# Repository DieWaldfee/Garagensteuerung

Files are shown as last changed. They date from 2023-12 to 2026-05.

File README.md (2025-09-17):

# Garagensteuerung
Steuerung eines Garagentorantriebs (Platine und Software) via Relaistrigger

### Beschreibung der Funktion:
Garagentorantriebe haben einen potentialfreien Relais-Kontakt. Wird dieser gebrückt, so wird der Antrieb aktiviert für eine Öffnen/Schließen -> das Tor fährt auf den nächsten Anschlag (oben oder unten). Wo das Tor aktuell steht und welche Richtung die Fahrt nehmen wird ist so nicht sensierbar.<br>
Im dazugekörigen blockly-Skript für ioBroker wird daher geprüft, welcher Endanschlag angefahren wird, um ggf. über einen weiteren Trigger (Triggerimpuls über das Relais) das Tor in die gewünschte Position zu bringen. Eine weitere Funktion ist - analog zu Rolladensteuerungen - eine Behanghöhe einzustellen. die wird über die Öffnungszeit / Schließzeit bestimmt -> 10% Behanghöhe entspricht damit 10% Öffnungszeit bis das Relais den Trigger zum stoppen des Torantriebs sendet- bzw. 90% Schließzeit, sollte das Tor am oberen Anschlag sein. (steht das Tor irgendwo, dann wird zuerst ein Anschlag angefahren, um dann den Behang einzustellen).

### Hardware:
Die Platine ist in dieser Version für eine Lochrasterplatine ausgelegt -> Leiterbahnen können mit einem Draht und Lötzinn erstellt werden. Dies ermöglicht es eigentlich jedem, der einen Lötkolben sein Eigen nennt es einfach nachzubauen :-) Die Eagle-Dateien liegen im Repository. Ein Überblick gibt das Fritzing-File. <br>
An der Platine können 4 Reed-Kontakte angeschlossen werden (oberer und unterer Anschlag, sowie zwei optionale Positionen). Über die Reedkontakte "Oben und Unten" wird die aktuelle Position des Tors bestimmt. Ein Relais dient dem Triggern des Garagenantriebs. Die STromversorgung kann entweder über ein Mini-Netzteil, oder einfach über ein USB-Netzteil realisiert werden (Letzteres ist bei mir im Einsatz). Drei LEDS zeigen ggf. Fehler, das Senden von MQTT-Botschaften und generell den Betrieb an. Optional kann ein DS18B20-Temperatursensor angeschlossen werden, sollte die Garagentemperatur von Interesse sein (weil der Wohnwagen dort steht, oder die Pflanzen überwintern sollen...).

### Software:
Der ESP32 benötigt natürlich seine Software. Das C++-File liegt im entsprechenden Verzeichnis und muss bezüglich MQTT-Broker-Account und Adresse angepasst werden. Zusätzlich ist natürlich auch das WiFi-Passwort und die IP-Adresse zu setzen. Danach kann das File z.B. mit der Arduino-IDE auf den ESP32DevKitV4-Modul aufgespielt werden. Compile und Upload brauchen nur ein paar Sekunden. Nach dem Start des ESP32 versucht der ESP32 den MQTT-Broker zu erreichen und übermittelt zyklisch den Status. Das angehängte blockly-Skript für den ioBroker liest die Botschaften aus und steuert das Tor an. Hier sind die Funktionen TorZu(um 23Uhr)... verortet. Der gesendete Torzustand kann im ioBroker zur Visualisierung verwendet werden. Ich steure den Telegramadapter an, sollte z.B. das Tor um 23Uhr nicht zu schließen sein (weil z.B. mein Sohn das Fahrad voll in den Fahrweg des Tores gestellt hat...).

### Abhängigkeiten:
OneWire.h:_____________OneWire by Jim Studt, Tom Pollard, Robin James... v2.3.8 (über Arduino IDE)<br>
DallasTemperature.h:___DallasTemperature by Miles Burton v4.0.3 (über Arduino IDE)<br>
WiFi.h:________________Arduino IDE<br>
WiFiClient.h:__________Arduino IDE<br>
PubSubClient.h:________PubSubClient by Nick O'Leary v2.8 (über Arduino IDE)<br>
esp_task_wdt.h:________Espressif IDE<br>

### Board ESP32
esp32 by Espressif Systems v1.0.6 (über Arduino IDE)<br>
Getestet habe ich auch v2.0.5<br>

### Benötigte Hardware:
* Relais <a href="https://www.amazon.de/gp/product/B0B5816YJ7/ref=ppx_yo_dt_b_search_asin_image?ie=UTF8&th=1"> Amazon </a> oder <a href="https://www.az-delivery.de/products/relais-modul"> AZ Delivery </a>
* ESP32 Dev Kit V4 <a href="https://www.azdelivery.de/products/esp-32-dev-kit-c-v4"> AZ Delivery </a>
* optional Temperatursensoren DS18B20 <a href="https://www.az-delivery.de/products/2er-set-ds18b20-mit-3m-kabel"> AZ Delivery </a>
* JST-Buchse <a href="https://www.amazon.de/gp/product/B0B2R99X99/ref=ppx_yo_dt_b_search_asin_title?ie=UTF8&psc=1"> Amazon </a>
* Klemmbuchse <a href="https://www.amazon.de/gp/product/B087RN8FDZ/ref=ppx_yo_dt_b_search_asin_title?ie=UTF8&th=1"> Amazon </a>
* Widerstände 4,7kOhm, 220 Ohm, 330 Ohm, Led grün, gelb und rot Amazon / eBay / Conrad...
* Levelshifter (3.3V <-> 5V)  <a href="https://www.amazon.de/RUNCCI-YUN-Pegelwandler-Converter-BiDirektional-Mikrocontroller/dp/B082F6BSB5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"> Amazon </a>
* Reed-Kontakte <a href="https://www.amazon.de/schwarz-Sicherheitskontaktsensor-magnetischer-Reed-Schalter-T%C3%BCrsensor/dp/B07Z4NCWDD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)"> Amazon </a>
* USB-Netzteil Amazon / eBay / Conrad...
* optional: Platinennetzteil AC-05-3    <a href="https://www.azdelivery.de/products/copy-of-220v-zu-5v-mini-netzteil"> AZ-Delivery </a>
* MC1490P (debouncer) auf Sockel, wenn gewünscht <a href="https://www.ebay.de/itm/201551880799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"> eBay </a>
* Kondensatoren <a href="https://www.amazon.de/AUKENIEN-Kondensator-Kondensatoren-Keramikkondensator-Kit/dp/B09NLZBC7R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"> Amazon </a>

**Haftungsausschluss**<br>
Deutsch: Dieses Projekt arbeitet mit Netzspannung (220 V) und darf ausschließlich von qualifiziertem Fachpersonal aufgebaut, installiert und betrieben werden. Durch die anliegende Spannung besteht Lebensgefahr! Fehler in Schaltung oder Software können zu Sachschäden (z. B. an Gebäude oder Heizung) oder zu gefährlichen Situationen für Leib und Leben führen. Nutzung auf eigene Gefahr – jegliche Haftung wird ausgeschlossen.
<br>
English: This project operates with mains voltage (220 V) and must only be assembled, installed, and operated by qualified professionals. The present voltage poses a risk of fatal electric shock! Errors in circuitry or software may cause property damage (e.g., to buildings or heating systems) or create life-threatening situations. Use at your own risk – any liability is disclaimed.

<br>(Bezugslinks füge ich später noch hinzu)

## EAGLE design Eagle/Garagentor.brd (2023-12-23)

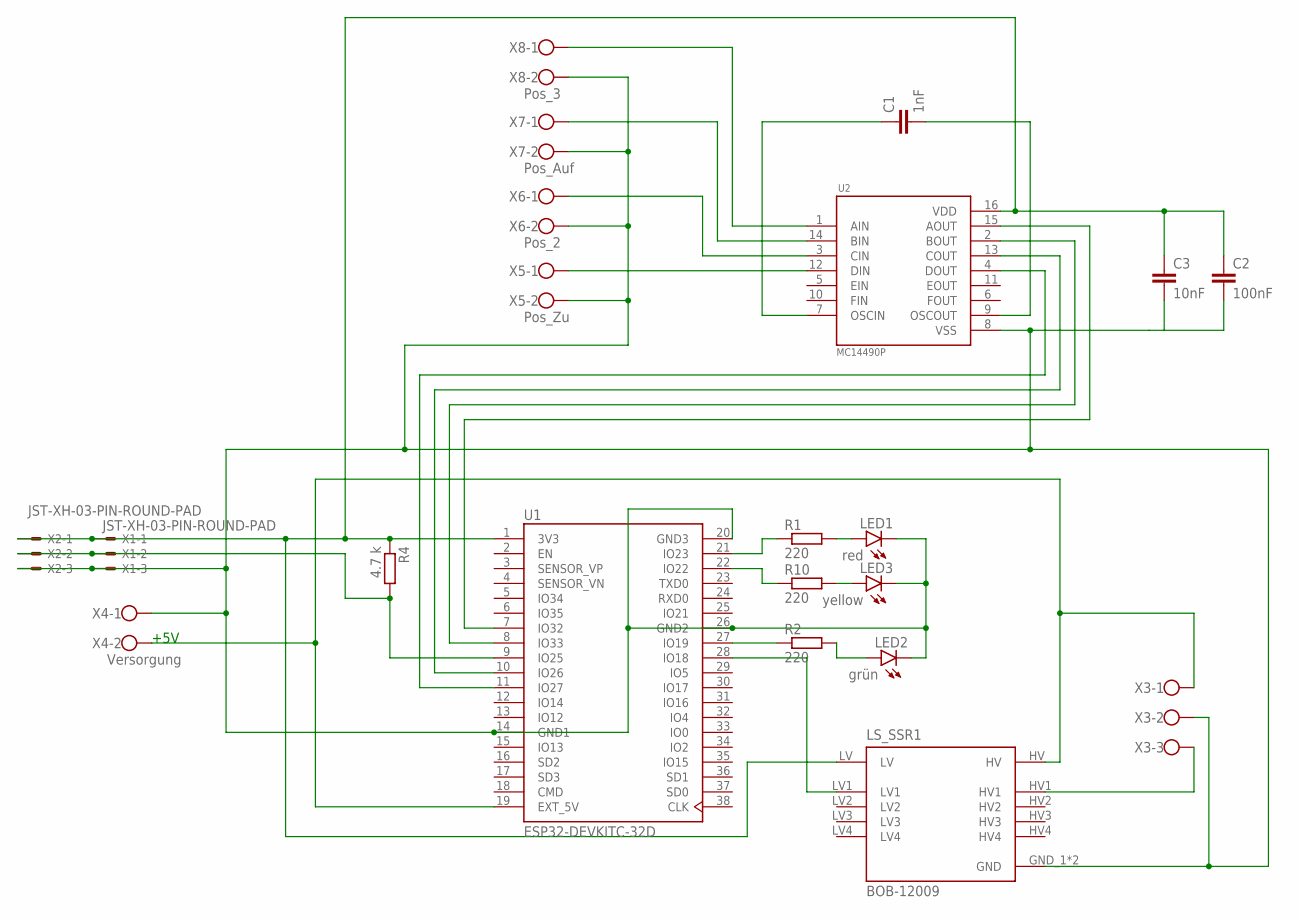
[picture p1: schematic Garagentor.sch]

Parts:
C1: 1nF; C050-024X044
C2: 100nF; C050-024X044
C3: 10nF; C050-024X044
LED1: red; LED3MM
LED2: grün; LED3MM
LED3: yellow; LED3MM
LS_SSR1: BOB-12009; CONV_BOB-12009
R1, R2, R10: 220; 0204/7
R4: 4.7 k; 0204/7
U1: ESP32-DEVKITC-32D; MODULE_ESP32-DEVKITC-32D
U2: MC14490P; DIP762W46P254L1918H444Q16P
X1, X2: JST-XH-03-PIN-ROUND-PAD; JST-XH-03-PACKAGE-ROUND-PAD
X3: W237-103
X4: Versorgung; W237-102
X5: Pos_Zu; W237-102
X6: Pos_2; W237-102
X7: Pos_Auf; W237-102
X8: Pos_3; W237-102

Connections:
GND$1: C2.2, C3.2, LED1.K (C), LED2.K (C), LED3.K (C), LS_SSR1.GND_1 (GND), LS_SSR1.GND_2 (GND), U1.14 (GND1), U1.20 (GND3), U1.26 (GND2), U2.8 (VSS), X1.3, X2.3, X3.2, X4.1, X5.2, X6.2, X7.2, X8.2
unnamed: R1.1, U1.21 (IO23)
unnamed: U1.7 (IO32), U2.15 (AOUT)
unnamed: R10.1, U1.22 (IO22)
unnamed: LED3.A, R10.2
unnamed: LS_SSR1.HV1, X3.3
unnamed: R2.1, U1.27 (IO19)
unnamed: LED1.A, R1.2
unnamed: LED2.A, R2.2
unnamed: U1.8 (IO33), U2.2 (BOUT)
unnamed: U1.10 (IO26), U2.13 (COUT)
unnamed: R4.2, U1.9 (IO25), X1.2, X2.2
unnamed: U1.11 (IO27), U2.4 (DOUT)
unnamed: U2.1 (AIN), X8.1
unnamed: U2.14 (BIN), X7.1
unnamed: U2.3 (CIN), X6.1
unnamed: LS_SSR1.LV1, U1.28 (IO18)
unnamed: U2.12 (DIN), X5.1
unnamed: C1.1, U2.7 (OSCIN)
unnamed: C1.2, U2.9 (OSCOUT)
VDD3$13: C2.1, C3.1, LS_SSR1.LV, R4.1, U1.1 (3V3), U2.16 (VDD), X1.1, X2.1
VDD5$3: LS_SSR1.HV, U1.19 (EXT_5V), X3.1, X4.2

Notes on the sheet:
+5V

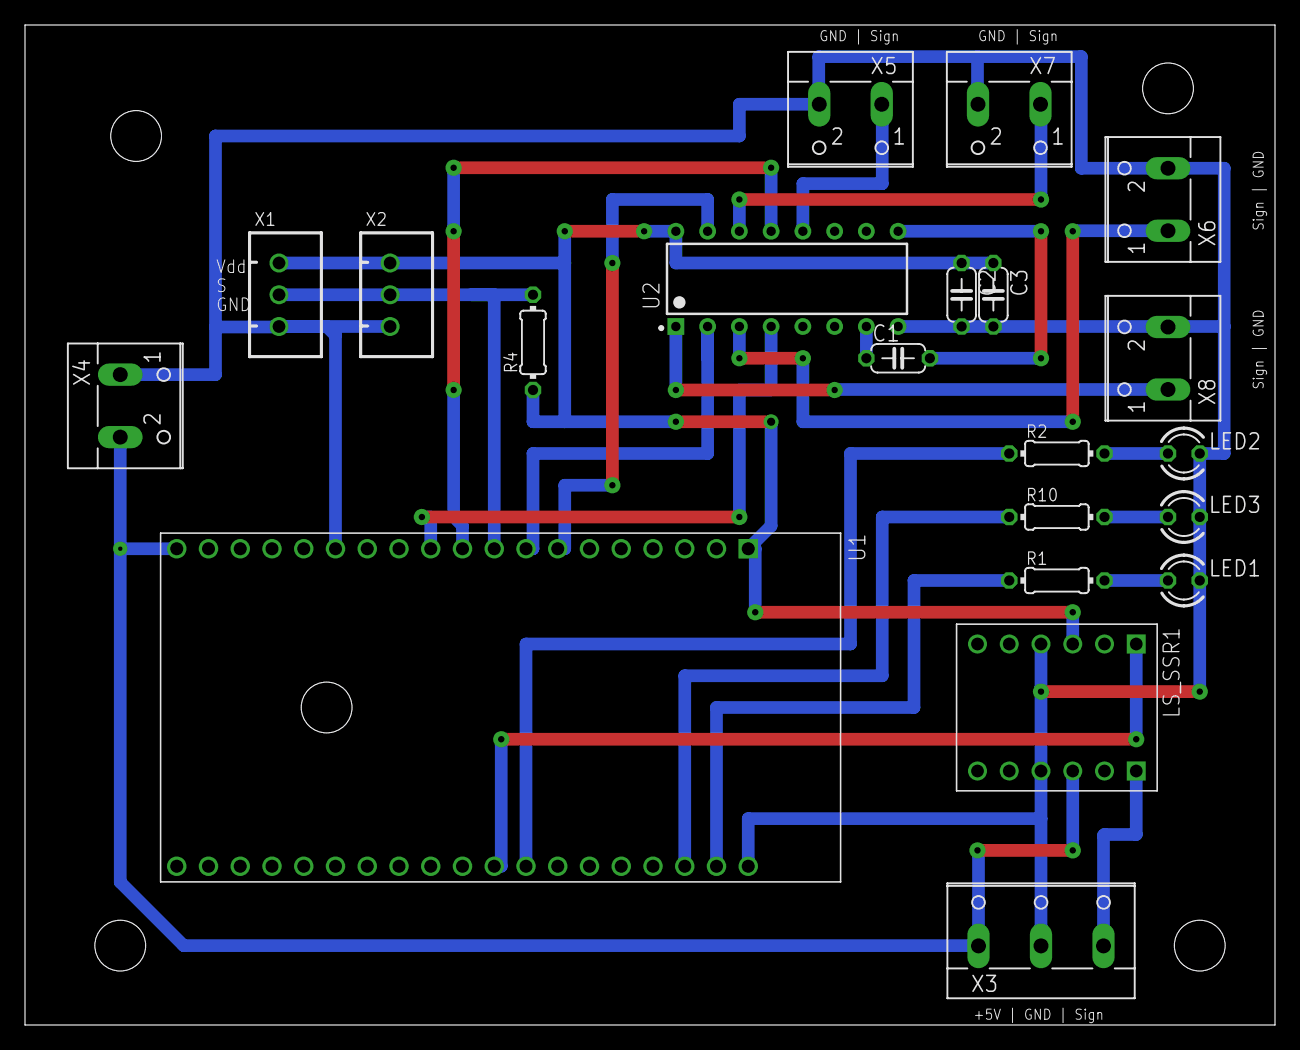
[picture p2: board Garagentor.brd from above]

Board: 2 copper layers, 100.0 x 80.0 mm, 21 parts (0 on the bottom side), 22 nets.

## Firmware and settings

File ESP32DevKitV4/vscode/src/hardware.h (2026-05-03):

// hardware.h
#pragma once

// ---------------------------------------------------------------------------
// Torspezifische Einstellungen
// ---------------------------------------------------------------------------
// Verfahrzeiten des Tors - diese Werte müssen an die individuellen Gegebenheiten angepasst werden
// Zeit in Sekunden, die das Tor zum vollständigen Öffnen (ZU -> AUF) bzw. Schließen (AUF -> ZU)
// benötigt. Die Zeit ist in Sekunden anzugeben und sollte mit einem realen Testlauf des Tors ermittelt
// werden. Ein geringer Zeitpuffer (z.B. 1s - je nach eingesetzter Torsteuerung) ist empfehlenswert,
// um die tatsächliche Bewegung des Tors und ggf. Totzeiten in der Torsteuerung zu berücksichtigen.
#define DEFAULT_TIME_TOR_AUF 15.0f
#define DEFAULT_TIME_TOR_ZU 20.0f
// Hysteresezeit bei schnellen Schaltvorgängen Zu-Zu, Auf-Auf oder schnellen Zu-Auf-Schaltungen
// Hier muss ggf. experimentell ermittelt werden. Anpassungen sind nur bei größeren Totzeiten
// in der Torantriebssteuerung nötig.
#define DEFAULT_TIME_HYSTERESE 1.0f

// ---------------------------------------------------------------------------
// Hardwarenahe Einstellungen
// ----------------------------------------------------------------------------
// Einstellungen für das Grundverhalten der Hardware
// Triggerteit = Zeit in ms, die das Relais für die Ansteuerung des Garagentors aktiviert wird
#define TRIGGERTIME 800  // 800ms Triggerzeit für das Garagentor

// Sensorreaktion der Magnetsensoren invertieren - ist herstellerabhängig ob NC oder NO
#define SENSORINVERT 1  // 0 = Magnetsensoren werden nicht invertiert; 1 = Sensoren werden invertiert

// Pinbelegung der Sensoren und Relais
// hier nichts ändern - siehe auch Schaltplan in der Projektbeschreibung
#define LED_ERROR 23
#define LED_MSG 22
#define LED_OK 19
#define REED1 27   // Tor-Zu-Sensor
#define REED2 26   // Zwischenstufe 1
#define REED3 32   // Zwischenstufe 2
#define REED4 33   // Tor-Auf-Sensor
#define RELAIS 18  // Relais zur Torsteuerung
#define ONE_WIRE_BUS 25

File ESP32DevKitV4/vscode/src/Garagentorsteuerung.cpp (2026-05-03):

// https://beelogger.de/sensoren/temperatursensor-ds18b20/ für Pinning und Anregung
#include <DallasTemperature.h>
#include <OneWire.h>
#include <PubSubClient.h>
#include <WiFi.h>
#include <WiFiClient.h>
#include <esp_task_wdt.h>

#include "hardware.h"
#include "secrets.h"

static byte debug = 1;
bool tempError = 0;  // tempError = 1 => keine DS18B20-Sensoren gefunden.
static String lastError = "";

// Definition der Zugangsdaten WiFi
WiFiClient myWiFiClient;

// Definition der Zugangsdaten MQTT
#define MQTT_CLIENTID "ESP32_Garagentorsteuerung"  // MQTT-ClientID - muss eindeutig im Netzwerk sein
#define GT_MQTT_KEEPALIVE 90
#define GT_MQTT_SOCKETTIMEOUT 30
#define MQTT_SERIAL_PUBLISH_STATUS "SmartHome/Garage/ESP32_Garagentorsteuerung/status"
#define MQTT_SERIAL_RECEIVER_COMMAND "SmartHome/Garage/ESP32_Garagentorsteuerung/command"
#define MQTT_SERIAL_PUBLISH_DS18B20 "SmartHome/Garage/ESP32_Garagentorsteuerung/Temperatur/"
#define MQTT_SERIAL_PUBLISH_STATE "SmartHome/Garage/ESP32_Garagentorsteuerung/state/"
#define MQTT_SERIAL_PUBLISH_CONFIG "SmartHome/Garage/ESP32_Garagentorsteuerung/config/"
#define MQTT_SERIAL_PUBLISH_BASIS "SmartHome/Garage/ESP32_Garagentorsteuerung/"
DeviceAddress myDS18B20Address;
unsigned long MQTTReconnect = 0;
#define MQTT_QUEUEDEPTH 50       // Tiefe der MQTT-Queue - 50 Botschaften
#define MQTT_QUEUEMAXWAITTIME 3  // Wartezeit für das Senden in eine Queue - danach Error!
struct MqttJob {                 // Struktur der MQTT-Queue
  char topic[128];               // topic:   Topic auf den die Botschaft gesendet werden soll -> 180 Zeichen lang
  char payload[256];             // payload: Botschaft, die an das Topic gesendet werden soll. -> 256 Zeichen max.
  bool retain;                   // retain:  true, wenn die Botschaft im Broker gespeichert bleibt und false, wenn
};  // nur die angemeldeten User die Botschaft erhalten - diese dann vergessen wird.
PubSubClient mqttClient(myWiFiClient);
static QueueHandle_t mqttQueue;  // Queuedefinition für die MQTT-Queue
static TaskHandle_t hmqtt;       // handler für den MQTT-Sender-Task
static SemaphoreHandle_t mutexMQTT;

// Zeitsteuerung für Tor auf und Tor zu
float timeTorAuf = DEFAULT_TIME_TOR_AUF;  // Gesamtzeit zum Öffnen des Garagentors [s]
float timeTorZu = DEFAULT_TIME_TOR_ZU;    // Gesamtzeit zum Schließen des Garagentors [s]
// Zeithysterese bei einer Auf-Auf-, Zu-Zu- oder schnellen Auf-Zu-Schaltung [s]
float timeHysterese = DEFAULT_TIME_HYSTERESE;
int volatile zustand = 0;       // aktuell gewünschte Toröffnung [0 = zu; 100 = auf; x -> Prozent Toröffnung über]
bool volatile positionZu = 0;   // Reed-Sensor 1 ist aktiv und Tor ist geschlossen
bool volatile positionAuf = 0;  // Reed-Sensor 4 ist aktiv und Tor ist vollständig offen
bool volatile position_2 = 0;   // Reed-Sensor 2 [optional] als Zwischenpositionsindikator (reine MQTT-Meldung)
bool volatile position_3 = 0;   // Reed-Sensor 3 [optional] als Zwischenpositionsindikator (reine MQTT-Meldung)

// Zustände
bool volatile torAuf = 0;  // Status der StateMaschine Zustand "TorAuf" - im Endanschlag - nächster Trigger -> Schließen
bool volatile torZu = 0;   // Status der StateMaschine Zustand "TorZu" - im Endanschlag - nächster Trigger -> Öffnen
bool volatile torUnDef = 0;  // Status der StateMaschine Zustand "TorUndefiniert" = irgendwas zwischen "Auf" und "Zu" &
                             // Fahrtrichtung bei Trigger ungekannt

// Warnstufen der angeschlossenen DS18B20 - Sensoren
float warnHighLevel = 30.0;         // obere Temperatur-Warnstufe bei Überschreitung
float warnLowLevel_1 = 5.0;         // untere Temperaturschwelle
float warnLowLevel_2 = 0.0;         // minimale Temperaturschwelle
bool volatile alertHighLevel = 0;   // Alarmschwelle HighLevel überschritten
bool volatile alertLowLevel_1 = 0;  // Alarmschwelle LowLevel_1 unterschritten
bool volatile alertLowLevel_2 = 0;  // Alarmschwelle LowLevel_2 unterschritten

// Initialisiere OneWire und Thermosensor(en)
OneWire oneWire(ONE_WIRE_BUS);
DallasTemperature myDS18B20(&oneWire);
int DS18B20_Count = 0;  // Anzahl der angeschlossenen Tempsensoren [0...n]

// Mutexdefinitionen
static SemaphoreHandle_t mutexTemp;
static SemaphoreHandle_t mutexStatus;
static SemaphoreHandle_t mutexTor;
static SemaphoreHandle_t mutexSensor;

// TaskRefrechTime
#define MQTTStateRefresh 20000  // Alle 20.000 Ticks = 20sec

// TaskHandler zur Verwendung mit ESP watchdog
static TaskHandle_t hgetTempFromSensor;
static TaskHandle_t hMQTTwatchdog;

// Queue-Definition für Torsteuerung
#define QUEUEDEPTH 10       // Tiefe der Queue - 10 Schaltvorgänge einer Phase für 5s
#define QUEUEMAXWAITTIME 3  // Wartezeit für das Senden in eine Queue - danach Error!
typedef struct {            // Struktur der Queue-Daten des Zustandes
  TickType_t ticktime;      // gewünchte TickTime der Phasenprüfung
  int zustand;              // geschalteter Zustand 0-100%
} s_queueData;
static QueueHandle_t torZustand;  // Queue-Handler für den gewünschten Torzustand (offen / geschlossen)
static QueueHandle_t qRelais;     // Queue-Handler für den Schaltzustand des Relais - Steuerung der Zeit für Bewegungen

// erforderliche Funtions-Prototypen
bool mqttPublishQueue(const char*, const char*, bool);

//-------------------------------------
// Basisfunktion zum sicheren Reset
void safeReset() {
  Serial.println("ESP32 Reset wird vorbereitet...");
  // Sauberes MQTT-Disconnect nur wenn Mutexe existieren (d.h. nicht während setup()-Phase).
  // Ohne diese Prüfung: xSemaphoreTake(NULL) → Assert-Crash wenn safeReset() aus mqttConnect()
  // heraus aufgerufen wird, bevor die Mutex-Initialisierung in setup() stattgefunden hat.
  if (mutexMQTT != nullptr) {
    Serial.println("MQTT Disconnect...");
    xSemaphoreTake(mutexMQTT, pdMS_TO_TICKS(1000));  // best-effort; kein assert - Reboot folgt
    mqttClient.disconnect();
    // kein xSemaphoreGive - blockiert alle MQTT-Operationen anderer Tasks bis Reboot
    delay(50);
    Serial.println("Flush TCP-Buffer...");
    myWiFiClient.clear();
    delay(50);
  }
  Serial.println("ESP32 Reset!");
  ESP.restart();
}

//-------------------------------------
// Formatiert eine DS18B20-Geräteadresse als lesbaren Hex-String
String formatDS18B20Address(const DeviceAddress addr) {
  String result = "";
  for (uint8_t j = 0; j < 8; j++) {
    result += "0x";
    if (addr[j] < 0x10) result += "0";
    result += String(addr[j], HEX);
    if (j < 7) result += ", ";
  }
  return result;
}

//-------------------------------------
// Callback für MQTT
void mqttCallback(char* topic, byte* message, unsigned int length) {
  BaseType_t rc;
  String str;
  String mqttMessage;
  String mqttTopicAC;
  byte tx_ac = 1;

  for (int i = 0; i < length; i++) {
    str += (char)message[i];
  }
  if (debug > 1) {
    Serial.print("Nachricht aus dem Topic: ");
    Serial.print(topic);
    Serial.print(". Nachricht: ");
    Serial.println(str);
  }
  // Test-Botschaften
  mqttTopicAC = MQTT_SERIAL_PUBLISH_BASIS;
  mqttTopicAC += "ac";
  if (str.startsWith("Test")) {
    if (debug) Serial.println("Test -> Test OK");
    mqttPublishQueue(mqttTopicAC.c_str(), "Test OK", false);
    tx_ac = 0;
  }

  // Mutex holen
  rc = xSemaphoreTake(mutexStatus, portMAX_DELAY);
  assert(rc == pdPASS);

  // debug-Modfikation
  if ((tx_ac) && (str.startsWith("debug=0"))) {
    debug = 0;
    mqttPublishQueue(mqttTopicAC.c_str(), "debug=0 umgesetzt", false);
    tx_ac = 0;
  }
  if ((tx_ac) && (str.startsWith("debug=1"))) {
    debug = 1;
    mqttPublishQueue(mqttTopicAC.c_str(), "debug=1 umgesetzt", false);
    tx_ac = 0;
  }
  if ((tx_ac) && (str.startsWith("debug=2"))) {
    debug = 2;
    mqttPublishQueue(mqttTopicAC.c_str(), "debug=2 umgesetzt", false);
    tx_ac = 0;
  }
  if ((tx_ac) && (str.startsWith("debug=3"))) {
    debug = 3;
    mqttPublishQueue(mqttTopicAC.c_str(), "debug=3 umgesetzt", false);
    tx_ac = 0;
  }
  // ErrorLED aus
  if ((tx_ac) && (str.startsWith("ErrorLED aus"))) {
    mqttMessage = "ErrorLED ausgeschaltet";
    digitalWrite(LED_ERROR, LOW);
    if (debug > 2) Serial.println(mqttMessage);
    mqttPublishQueue(mqttTopicAC.c_str(), mqttMessage.c_str(), false);
    tx_ac = 0;
  }
  // Tortrigger2 vor Tortrigger prüfen — startsWith("Tortrigger") würde sonst auch "Tortrigger2" matchen
  if ((tx_ac) && (str.startsWith("Tortrigger2"))) {
    mqttMessage = "Tortrigger2 ausgeführt";
    bool qData = true;
    BaseType_t rcQ;
    rcQ = xQueueSendToBack(qRelais, &qData, pdMS_TO_TICKS(100));
    if (debug > 2) Serial.println(mqttMessage);
    mqttPublishQueue(mqttTopicAC.c_str(), rcQ == pdPASS ? mqttMessage.c_str() : "Tortrigger2 FEHLER: Queue voll!",
                     false);
    tx_ac = 0;
  }
  if ((tx_ac) && (str.startsWith("Tortrigger"))) {
    mqttMessage = "Tortrigger ausgeführt";
    bool qData = true;
    BaseType_t rcQ;
    rcQ = xQueueSendToBack(qRelais, &qData, pdMS_TO_TICKS(100));
    if (debug > 2) Serial.println(mqttMessage);
    mqttPublishQueue(mqttTopicAC.c_str(), rcQ == pdPASS ? mqttMessage.c_str() : "Tortrigger FEHLER: Queue voll!",
                     false);
    tx_ac = 0;
  }
  if ((tx_ac) && (str.startsWith("state="))) {
    BaseType_t rcQ;
    s_queueData qData;
    str.remove(0, 6);
    qData.zustand = constrain(str.toInt(), 0, 100);
    qData.ticktime = xTaskGetTickCount();
    rcQ = xQueueSendToBack(torZustand, &qData, pdMS_TO_TICKS(100));
    if (rcQ == pdPASS) {
      mqttMessage = "state=";
      mqttMessage += String(qData.zustand);
      mqttMessage += " umgesetzt";
    } else {
      mqttMessage = "state= FEHLER: Queue voll!";
    }
    if (debug > 2) Serial.println(mqttMessage);
    mqttPublishQueue(mqttTopicAC.c_str(), mqttMessage.c_str(), false);
    tx_ac = 0;
  }
  if ((tx_ac) && (str.startsWith("restart") || str.startsWith("reboot"))) {
    // Kein Mutex nötig: Callback wird von mqttSender aufgerufen, das mutexMQTT bereits hält
    mqttClient.publish(mqttTopicAC.c_str(), "reboot in einer Sekunde!");
    if (debug) Serial.println("für Restart: alles aus & restart in 1s!");
    digitalWrite(RELAIS, HIGH);  // Relais sicherstellen: aus
    digitalWrite(LED_OK, LOW);
    digitalWrite(LED_ERROR, HIGH);
    vTaskDelay(1000);
    if (debug) Serial.println("führe Restart aus!");
    safeReset();
  }
  // Free Mutex
  rc = xSemaphoreGive(mutexStatus);
  assert(rc == pdPASS);
}

//-------------------------------------
// Subfunktionen für MQTT-Status-Task
// MQTT DS18B20 Status senden
void printDS18B20MQTT() {
  String mqttTopic;
  String mqttJson;
  String mqttPayload;
  int i;
  for (i = 0; i < DS18B20_Count; i++) {
    myDS18B20.getAddress(myDS18B20Address, i);
    String adresse = formatDS18B20Address(myDS18B20Address);
    float tempVal = myDS18B20.getTempCByIndex(i);  // einmalig lesen – JSON und Topic bleiben konsistent
    // JSON
    mqttTopic = MQTT_SERIAL_PUBLISH_DS18B20 + String(i) + "/JSON";
    mqttJson = "{\"ID\":\"" + String(i) + "\"";
    mqttJson += ",\"Temperatur\":\"" + String(tempVal) + "\"";
    mqttJson += ",\"Adresse\":\"(" + adresse + ")\"}";
    if (debug > 2) Serial.println("MQTT_JSON: " + mqttJson);
    mqttPublishQueue(mqttTopic.c_str(), mqttJson.c_str(), false);
    // Temperatur
    mqttTopic = MQTT_SERIAL_PUBLISH_DS18B20 + String(i) + "/Temperatur";
    mqttPayload = String(tempVal);
    mqttPublishQueue(mqttTopic.c_str(), mqttPayload.c_str(), false);
    if (debug > 2) Serial.print("MQTT ID: ");
    if (debug > 2) Serial.println(mqttPayload);
    // ID
    mqttTopic = MQTT_SERIAL_PUBLISH_DS18B20 + String(i) + "/ID";
    mqttPayload = String(i);
    mqttPublishQueue(mqttTopic.c_str(), mqttPayload.c_str(), false);
    if (debug > 2) Serial.print("MQTT Temperatur: ");
    if (debug > 2) Serial.println(mqttPayload);
    // Adresse
    mqttTopic = MQTT_SERIAL_PUBLISH_DS18B20 + String(i) + "/Adresse";
    mqttPublishQueue(mqttTopic.c_str(), adresse.c_str(), false);
    if (debug > 2) Serial.print("MQTT Adresse: ");
    if (debug > 2) Serial.println(adresse);
  }
}

// MQTT Status Betrieb senden
void printStateMQTT() {
  String mqttTopic;
  String mqttJson;
  String mqttPayload;
  String wifiRSSI = (WiFi.status() == WL_CONNECTED) ? String(WiFi.RSSI()) : String("--");
  mqttTopic = MQTT_SERIAL_PUBLISH_STATE;
  mqttTopic += "JSON_0";
  mqttJson = "{\"lastError\":\"" + String(lastError) + "\"";
  mqttJson += ",\"WiFi_Signal_Strength\":\"" + wifiRSSI + "\"";
  mqttJson += ",\"WiFi_IP_Adress\":\"" + WiFi.localIP().toString() + "\"";
  mqttJson += ",\"WiFi_MAC_Adress\":\"" + WiFi.macAddress() + "\"";
  mqttJson += ",\"Torzustand_Prozent\":\"" + ((zustand >= 0) ? String(zustand) + " %" : String("unbekannt")) + "\"";
  mqttJson += ",\"Zustand\":\"";
  if (torAuf == 1)
    mqttJson += "Tor offen\"}";
  else if (torZu == 1)
    mqttJson += "Tor geschlossen\"}";
  else if (torUnDef == 1)
    mqttJson += "Torzustand unklar\"}";
  else
    mqttJson += "unbekannt\"}";
  if (debug > 2) Serial.println("MQTT_JSON: " + mqttJson);
  mqttPublishQueue(mqttTopic.c_str(), mqttJson.c_str(), false);
  mqttTopic = MQTT_SERIAL_PUBLISH_STATE;
  mqttTopic += "JSON_1";
  mqttJson = "{\"SensorPositionZu\":\"" + String(positionZu) + "\"";
  mqttJson += ",\"SensorPositionAuf\":\"" + String(positionAuf) + "\"";
  mqttJson += ",\"SensorPosition2\":\"" + String(position_2) + "\"";
  mqttJson += ",\"SensorPosition3\":\"" + String(position_3) + "\"}";
  if (debug > 2) Serial.println("MQTT_JSON: " + mqttJson);
  mqttPublishQueue(mqttTopic.c_str(), mqttJson.c_str(), false);
  mqttTopic = MQTT_SERIAL_PUBLISH_STATE;
  mqttTopic += "JSON_2";
  mqttJson = "{\"alertHighLevel\":\"" + String(alertHighLevel) + "\"";
  mqttJson += ",\"alertLowLevel_1\":\"" + String(alertLowLevel_1) + "\"";
  mqttJson += ",\"alertLowLevel_2\":\"" + String(alertLowLevel_2) + "\"";
  mqttJson += ",\"tempError\":\"" + String(tempError) + "\"}";
  if (debug > 2) Serial.println("MQTT_JSON: " + mqttJson);
  mqttPublishQueue(mqttTopic.c_str(), mqttJson.c_str(), false);
  // lastError
  mqttTopic = MQTT_SERIAL_PUBLISH_STATE;
  mqttTopic += "lastError";
  mqttPayload = lastError;
  mqttPublishQueue(mqttTopic.c_str(), mqttPayload.c_str(), false);
  if (debug > 2) Serial.print("MQTT lastError: ");
  if (debug > 2) Serial.println(mqttPayload);
  // WiFi Signalstärke
  mqttTopic = MQTT_SERIAL_PUBLISH_STATE;
  mqttTopic += "WiFi_Signal_Strength";
  mqttPayload = wifiRSSI;
  mqttPublishQueue(mqttTopic.c_str(), mqttPayload.c_str(), false);
  if (debug > 2) Serial.print("WiFi Signalstärke: ");
  if (debug > 2) Serial.println(mqttPayload);
  // WiFi IP-Adresse
  mqttTopic = MQTT_SERIAL_PUBLISH_STATE;
  mqttTopic += "WiFi_IP_Adress";
  mqttPayload = WiFi.localIP().toString();
  mqttPublishQueue(mqttTopic.c_str(), mqttPayload.c_str(), false);
  if (debug > 2) Serial.print("WiFi IP-Adresse: ");
  if (debug > 2) Serial.println(mqttPayload);
  // WiFi MAC-Adresse
  mqttTopic = MQTT_SERIAL_PUBLISH_STATE;
  mqttTopic += "WiFi_MAC_Adress";
  mqttPayload = WiFi.macAddress();
  mqttPublishQueue(mqttTopic.c_str(), mqttPayload.c_str(), false);
  if (debug > 2) Serial.print("WiFi MAC-Adresse: ");
  if (debug > 2) Serial.println(mqttPayload);
  // Tor Zustand in Prozent
  mqttTopic = MQTT_SERIAL_PUBLISH_STATE;
  mqttTopic += "Torzustand_Prozent";
  mqttPayload = (zustand >= 0) ? String(zustand) + " %" : "unbekannt";
  mqttPublishQueue(mqttTopic.c_str(), mqttPayload.c_str(), false);
  if (debug > 2) Serial.print("Torzustand [%]: ");
  if (debug > 2) Serial.println(mqttPayload);
  // Torstatus
  mqttTopic = MQTT_SERIAL_PUBLISH_STATE;
  mqttTopic += "Zustand";
  mqttPayload = "Torzustand Fehler!";
  if (torAuf == 1) mqttPayload = "Tor offen";
  if (torZu == 1) mqttPayload = "Tor geschlossen";
  if (torUnDef == 1) mqttPayload = "Torzustand unklar";
  mqttPublishQueue(mqttTopic.c_str(), mqttPayload.c_str(), false);
  if (debug > 2) Serial.print("Zustand: ");
  if (debug > 2) Serial.println(mqttPayload);
  // Sensor Status "Zu"
  mqttTopic = MQTT_SERIAL_PUBLISH_STATE;
  mqttTopic += "SensorPositionZu";
  mqttPayload = positionZu;
  mqttPublishQueue(mqttTopic.c_str(), mqttPayload.c_str(), false);
  if (debug > 2) Serial.print("Sensor Position_Zu: ");
  if (debug > 2) Serial.println(mqttPayload);
  // Sensor Status "Auf"
  mqttTopic = MQTT_SERIAL_PUBLISH_STATE;
  mqttTopic += "SensorPositionAuf";
  mqttPayload = positionAuf;
  mqttPublishQueue(mqttTopic.c_str(), mqttPayload.c_str(), false);
  if (debug > 2) Serial.print("Sensor Position_Auf: ");
  if (debug > 2) Serial.println(mqttPayload);
  // Sensor Status "2"
  mqttTopic = MQTT_SERIAL_PUBLISH_STATE;
  mqttTopic += "SensorPosition2";
  mqttPayload = position_2;
  mqttPublishQueue(mqttTopic.c_str(), mqttPayload.c_str(), false);
  if (debug > 2) Serial.print("Sensor Position_2: ");
  if (debug > 2) Serial.println(mqttPayload);
  // Sensor Status "3"
  mqttTopic = MQTT_SERIAL_PUBLISH_STATE;
  mqttTopic += "SensorPosition3";
  mqttPayload = position_3;
  mqttPublishQueue(mqttTopic.c_str(), mqttPayload.c_str(), false);
  if (debug > 2) Serial.print("Sensor Position_3: ");
  if (debug > 2) Serial.println(mqttPayload);
  // alertHighLevel
  mqttTopic = MQTT_SERIAL_PUBLISH_STATE;
  mqttTopic += "alertHighLevel";
  mqttPayload = alertHighLevel;
  mqttPublishQueue(mqttTopic.c_str(), mqttPayload.c_str(), false);
  if (debug > 2) Serial.print("alertHighLevel: ");
  if (debug > 2) Serial.println(mqttPayload);
  // alertLowLevel_1
  mqttTopic = MQTT_SERIAL_PUBLISH_STATE;
  mqttTopic += "alertLowLevel_1";
  mqttPayload = alertLowLevel_1;
  mqttPublishQueue(mqttTopic.c_str(), mqttPayload.c_str(), false);
  if (debug > 2) Serial.print("alertLowLevel_1: ");
  if (debug > 2) Serial.println(mqttPayload);
  // alertLowLevel_2
  mqttTopic = MQTT_SERIAL_PUBLISH_STATE;
  mqttTopic += "alertLowLevel_2";
  mqttPayload = alertLowLevel_2;
  mqttPublishQueue(mqttTopic.c_str(), mqttPayload.c_str(), false);
  if (debug > 2) Serial.print("alertLowLevel_2: ");
  if (debug > 2) Serial.println(mqttPayload);
  // tempError
  mqttTopic = MQTT_SERIAL_PUBLISH_STATE;
  mqttTopic += "tempError";
  mqttPayload = tempError;
  mqttPublishQueue(mqttTopic.c_str(), mqttPayload.c_str(), false);
  if (debug > 2) Serial.print("tempError: ");
  if (debug > 2) Serial.println(mqttPayload);
}
// MQTT Config und Parameter senden
void printConfigMQTT() {
  String mqttTopic;
  String mqttJson;
  String mqttPayload;
  // Teil 1
  mqttTopic = MQTT_SERIAL_PUBLISH_CONFIG;
  mqttTopic += "JSON_0";
  mqttJson = "{\"timeTorAuf\":\"" + String(timeTorAuf) + "\"";
  mqttJson += ",\"timeTorZu\":\"" + String(timeTorZu) + "\"";
  mqttJson += ",\"timeHysterese\":\"" + String(timeHysterese) + "\"";
  mqttJson += ",\"warnHighLevel\":\"" + String(warnHighLevel) + "\"";
  mqttJson += ",\"warnLowLevel_1\":\"" + String(warnLowLevel_1) + "\"";
  mqttJson += ",\"warnLowLevel_2\":\"" + String(warnLowLevel_2) + "\"";
  mqttJson += ",\"debug\":\"" + String(debug) + "\"}";
  if (debug > 2) Serial.println("MQTT_JSON: " + mqttJson);
  mqttPublishQueue(mqttTopic.c_str(), mqttJson.c_str(), false);
  // timeTorAuf
  mqttTopic = MQTT_SERIAL_PUBLISH_CONFIG;
  mqttTopic += "timeTorAuf";
  mqttPayload = timeTorAuf;
  mqttPublishQueue(mqttTopic.c_str(), mqttPayload.c_str(), false);
  if (debug > 2) Serial.print("timeTorAuf: ");
  if (debug > 2) Serial.println(mqttPayload);
  // timeTorZu
  mqttTopic = MQTT_SERIAL_PUBLISH_CONFIG;
  mqttTopic += "timeTorZu";
  mqttPayload = timeTorZu;
  mqttPublishQueue(mqttTopic.c_str(), mqttPayload.c_str(), false);
  if (debug > 2) Serial.print("timeTorZu: ");
  if (debug > 2) Serial.println(mqttPayload);
  // timeHysterese
  mqttTopic = MQTT_SERIAL_PUBLISH_CONFIG;
  mqttTopic += "timeHysterese";
  mqttPayload = timeHysterese;
  mqttPublishQueue(mqttTopic.c_str(), mqttPayload.c_str(), false);
  if (debug > 2) Serial.print("timeHysterese: ");
  if (debug > 2) Serial.println(mqttPayload);
  // warnHighLevel
  mqttTopic = MQTT_SERIAL_PUBLISH_CONFIG;
  mqttTopic += "warnHighLevel";
  mqttPayload = warnHighLevel;
  mqttPublishQueue(mqttTopic.c_str(), mqttPayload.c_str(), false);
  if (debug > 2) Serial.print("warnHighLevel: ");
  if (debug > 2) Serial.println(mqttPayload);
  // warnLowLevel_1
  mqttTopic = MQTT_SERIAL_PUBLISH_CONFIG;
  mqttTopic += "warnLowLevel_1";
  mqttPayload = warnLowLevel_1;
  mqttPublishQueue(mqttTopic.c_str(), mqttPayload.c_str(), false);
  if (debug > 2) Serial.print("warnLowLevel_1: ");
  if (debug > 2) Serial.println(mqttPayload);
  // warnLowLevel_2
  mqttTopic = MQTT_SERIAL_PUBLISH_CONFIG;
  mqttTopic += "warnLowLevel_2";
  mqttPayload = warnLowLevel_2;
  mqttPublishQueue(mqttTopic.c_str(), mqttPayload.c_str(), false);
  if (debug > 2) Serial.print("warnLowLevel_2: ");
  if (debug > 2) Serial.println(mqttPayload);
  // debug
  mqttTopic = MQTT_SERIAL_PUBLISH_CONFIG;
  mqttTopic += "debug";
  mqttPayload = debug;
  mqttPublishQueue(mqttTopic.c_str(), mqttPayload.c_str(), false);
  if (debug > 2) Serial.print("debug: ");
  if (debug > 2) Serial.println(mqttPayload);
}
// LED-Blik-OK
void LEDblinkMsg() {
  digitalWrite(LED_MSG, HIGH);
  delay(150);
  digitalWrite(LED_MSG, LOW);
}
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
void loop() {
  // loop wird als Task nicht gebraucht
  vTaskDelete(nullptr);
}

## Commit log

2023-12-23 Add files via upload
    ESP32 code hinzugefügt
2023-12-23 Add files via upload
    Fritzing hinzugefügt
    [Garagentorsteuerung.fzz]
2023-12-23 Add files via upload
    Eagle files hinzugefügt
    [Garagentor.brd, Garagentor.sch]
2023-12-23 Update README.md
    Optik der Überschriften
2026-05-03 code redesign & robustness
    [Garagentorsteuerung.cpp, hardware.h]
